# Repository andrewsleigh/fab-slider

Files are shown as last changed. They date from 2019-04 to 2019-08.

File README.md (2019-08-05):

# Fab Slider

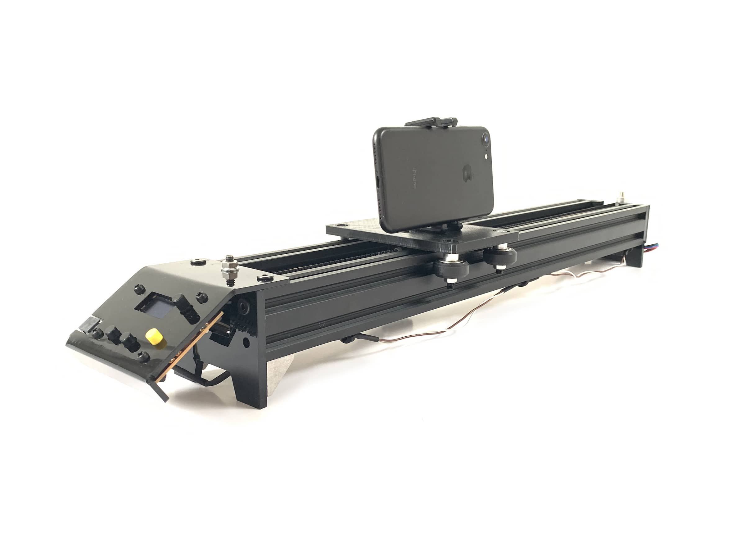
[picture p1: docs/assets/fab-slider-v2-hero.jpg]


A fab-able DIY motorised camera slider

* [The (Arduino Nano) microcontroller, user controls and TMC2130 stepper driver are all integrated onto one board here](boards/driver-arduino-shield/v3)
* [3D and 2D files for the assembly are all here](3d-parts/v1)
* [Arduino sketch here](arduino-code/v2)

This project is designed to be easily replicated, adapted or hacked on by anyone with access to typical fablab tools. 

It's primarily an exercise in learning: how to use a 3D printer; how use an Arduino; how to design circuit boards; how to assemble a machine, and so on. 

So really, it's all about the documentation, which is here:

* <https://andrewsleigh.com/fab-slider/>
* Or see [`docs/_posts/`](docs/_posts/) in this repo

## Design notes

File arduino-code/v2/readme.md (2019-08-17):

# Readme

## Recent changes

Some small modification following testing for version 2.1

* Slowed down timelapse speed range (from min 50 / max 250 to min 2 / max 50
* Changed GUI behaviour to include full information on settings (still non-interactive) while traversing
* Automatically switches directions after hitting end-stop

## State machine

Here is a diagram of the simpler state machine I'm building in this code:

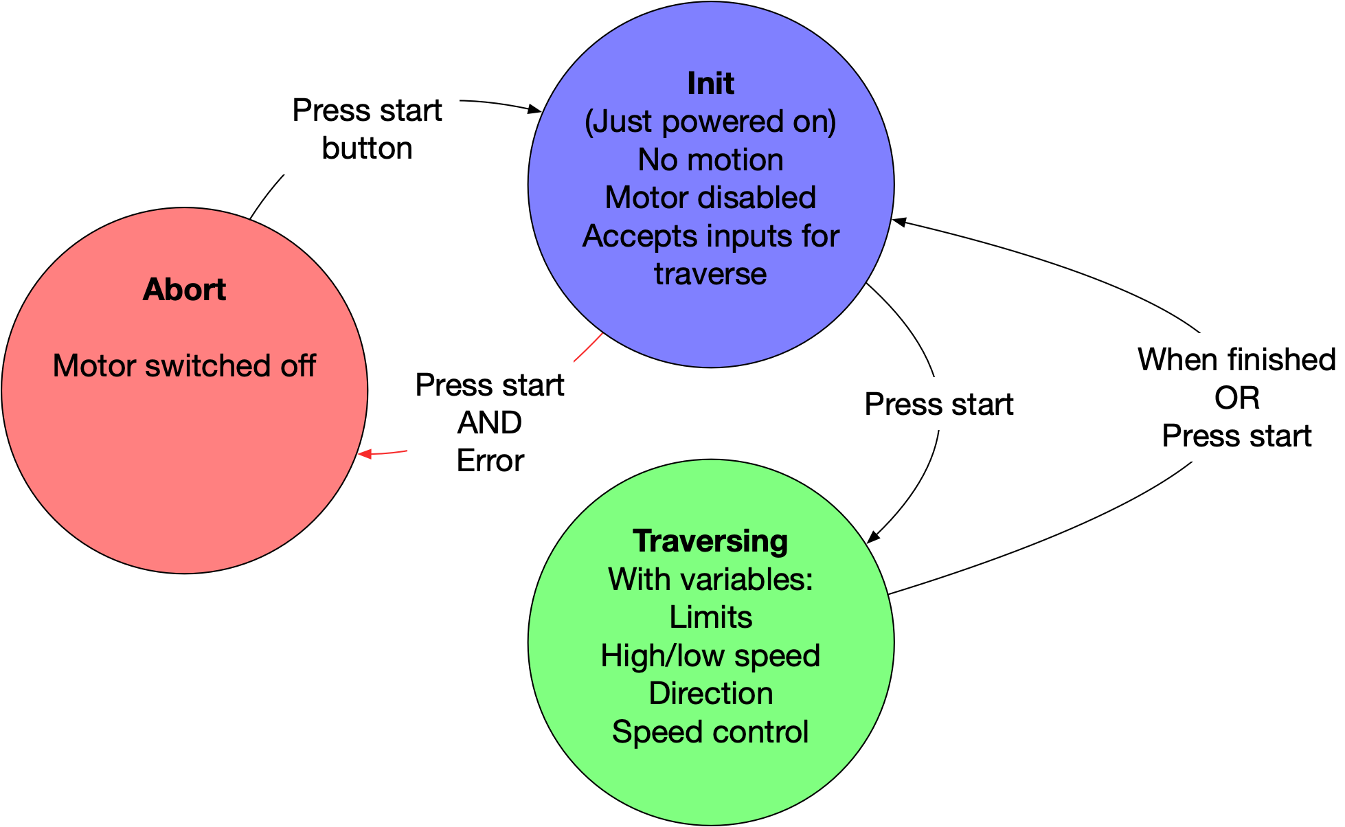
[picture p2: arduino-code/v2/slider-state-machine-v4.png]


<hr/>

This is a lightly documented version of the code for the first release version of my camera slider (v2 in this repo). This is much simplified from the old complex state machine (and quite similar to the v1 code). 

## Libraries

I'm using these Arduino libraries to handle motor control, non-blocking timers, button debouncing and OLED graphics respectively:

```
#include <AccelStepper.h>
#include <neotimer.h>
#include <Bounce2.h>

// OLED
#include <U8g2lib.h>
#include <SPI.h>
#include <Wire.h>
```

## User configuration

The variables that you might want to change are listed at the top of the file so speeds can be tweaked

```
int videoMinSpeed = 500;
int videoMaxSpeed = 5000;
int timelapseMinSpeed = 50;
int timelapseMaxSpeed = 250;
int endStopPadding = 300; // a safe distance to disengage the gantry from the end stops 
```

## Debugging setup

As documented in [Better debugging with the serial monitor](https://andrewsleigh.com/fab-slider/coding-better-debugging/) (or [GitHub link](https://github.com/andrewsleigh/fab-slider/blob/master/docs/_posts/2019-05-12-coding-better-debugging.md)), this section sets up the definitions that allow you to switch serial debugging on and off. You'd want to turn it off in use because sending all that data to the serial monitor interrupts the motion of the stepper.

```
String errorMessage = ""; // this string needs to be initialised even if we're not running debugging

// comment these out to remove debugging
//#define DEBUG // needed for all debugging
//#define DEBUG_TIMER // for messages that print every few seconds
//#define DEBUG_STATE_CHANGE // for messages that print only on a change in the machine state

#ifdef DEBUG

// set up debug timer
Neotimer statusUpdateTimer = Neotimer();

// set up string messages
#define DEBUG_PRINT(str)    \
  Serial.print(str); \
  Serial.print(" ------ ");      \
  Serial.print("In ");    \
  Serial.print(__PRETTY_FUNCTION__); \
  Serial.print(", line: ");      \
  Serial.println(__LINE__);     \

#else
#define DEBUG_PRINT(str) // just leaves an empty definition without serial printing
#endif

```

## Creating objects and variables

After that we just setup all the objects and variables we'll use later. These settings are tweaked for the new shield I designed for an Arduino Nano board and TMC2130 driver.

```
// Accelstepper object
// Revised for nano shield. Format: interface, step pin, direction pin
AccelStepper stepper(AccelStepper::DRIVER, 3, 2);

// Instantiate Bounce objects for buttons
Bounce debouncer_start = Bounce();
Bounce debouncer_mode = Bounce();
Bounce debouncer_direction = Bounce();

// define input/button pin numbers
const int startButtonPin = A3;
const int leftEndStopPin = 6;
const int rightEndStopPin = 5;
const int startFromLeftPin = 7;
const int isTimelapseSpeedPin = 8;

// define output pin numbers
const int motorOffPin = 4;

// define analogue input for speed knob
const int speedPotPin = A2; // revised for nano
int speedInput = 0; // a variable to stare it in
int traverseSpeed = 0; // variable to hold speed when calculated

// variables to determine kind of traverse
bool startFromLeft = true;
bool isTimelapseSpeed = false;

```

## Setup state machine

As part of this, there is a section for the state machine itself:

```
// WARNING: values, order of items and total number of items must match the array below
enum possibleStates {
  INIT,
  TRAVERSING,
  ABORTED
};

// create an array of labels from the enum for debugging
// WARNING: this array must be updated if you change the enum
String stateLabels[3] = {
  "INIT",
  "TRAVERSING",
  "ABORTED"
};

// create a variable of this type
enum possibleStates currentState;

// keep track of whether the state has changed to limit status message updates
bool isNewState;
```

## Initialise OLED Library

My OLED module has I2C pins, so it's important to use the `HW_I2C` keyword in the constructor. I intially used the software I2C mode and it made everything run very slowly. 

Also, after much troubleshooting, I found that I had to initialise the variable that sets the width of the speed indicator on screen up here. If I initialised it inside the `loop()` where I was handling the screen drawing, bad things happened.

```
// OLED library constructor
// Use hardware I2C to avoid code running like treacle
U8G2_SSD1306_128X64_NONAME_2_HW_I2C u8g2 (U8G2_R0, A5, A4);

// instantiate variable to hold width of speed indicator bar. Seems to cuase problems if you create this at the point of use.
float speedBoxWidth = 5;
```

## Setup()

In `setup()` we:
* Set values for the motor
* Set values for the timer
* Open serial comms, if debugging is enabled
* Set up the switches with internal pullup resistors (so they're pulled low to activate)
* Set up output pins for the motor enable function
* Use the debounce library to set up our push-buttons
* Set the starting state, ready for the loop
* Setup the OLED screen ("[This function will reset, configure, clear and disable power save mode of the display](https://github.com/olikraus/u8g2/wiki/u8g2reference#begin)")

```
void setup() {
  stepper.setMaxSpeed(4000); // See https://forum.arduino.cc/index.php?topic=487134.0
  stepper.setAcceleration(2000.0);

#ifdef DEBUG
  Serial.begin(9600); // serial comms for debugging

  // set up  debug message timer
  statusUpdateTimer.set(2000);
#endif

  // initialize the button pins as inputs:
  pinMode(leftEndStopPin, INPUT_PULLUP);
  pinMode(rightEndStopPin, INPUT_PULLUP);

  // initialise output pin
  pinMode(motorOffPin, OUTPUT);

  // Debounced buttons
  debouncer_start.attach(startButtonPin, INPUT_PULLUP); // Attach the debouncer to a pin with INPUT_PULLUP mode
  debouncer_start.interval(25); // Use a debounce interval of 25 milliseconds
  debouncer_direction.attach(startFromLeftPin, INPUT_PULLUP);
  debouncer_direction.interval(25);
  debouncer_mode.attach(isTimelapseSpeedPin, INPUT_PULLUP);
  debouncer_mode.interval(25);

  // set startup state
  currentState = INIT;
  isNewState = true;

  // OLED
  u8g2.begin();
}  
```

## Loop()

Inside the main loop, we first check the state of the push-buttons.

Then we switch through all of the possible machine states, printing any debug messages if required, calling the functions for that state, and checking to see if the push button has been pressed in case we need to switch to a different state. All the OLED drawing is also handled inside this loop 

After the state machine switch, we just check to see if continuous debug messages need to be printed.

```
void loop() {

  // Debounced  buttons
  debouncer_start.update(); // Update the Bounce instance
  debouncer_mode.update();
  debouncer_direction.update();

  switch (currentState) {
    case INIT:

#ifdef DEBUG_STATE_CHANGE
      if (isNewState) {
        printDebugMessages();
        isNewState = false;
      }
#endif

      switchOffMotor();      // disable motor until we need it

      getControlInputs();    // get values for all the motion control variables

      // OLED
      speedBoxWidth = map(analogRead(speedPotPin), 0, 1023, 124, 4); // reverse the reading from the pot because it's wired up the other way around
      // reduce resolution to avoid jittery display
      speedBoxWidth = round(speedBoxWidth / 4);
      speedBoxWidth = speedBoxWidth * 4;

      u8g2.firstPage();
      do {
        u8g2.setFont(u8g2_font_helvB14_tr);
        u8g2.drawStr(0, 14, "Ready");
        u8g2.setFont(u8g2_font_helvB08_tr); // monospace
        // Speed
        u8g2.drawRFrame(0, 22, 128, 16, 3);
        u8g2.drawRBox(2, 24, speedBoxWidth, 12, 1);
        // mode backgrounds
        u8g2.drawBox(0, 42, 62, 15);
        u8g2.drawTriangle(12, 56,  20, 64,  28, 56);
        u8g2.drawBox(66, 42, 62, 15);
        u8g2.drawTriangle(100, 56,  108, 64,  116, 56);
        u8g2.setDrawColor(0);
        if (isTimelapseSpeed) {
          u8g2.setCursor(70, 53); // different padding for each string
          u8g2.print("Timelapse");
        } else {
          u8g2.setCursor(82, 53);
          u8g2.print("Video");
        }

        u8g2.setCursor(13, 53); // add some padding to the left
        if (startFromLeft) {
          u8g2.print("L >> R");
        } else {
          u8g2.print("R >> L");
        }

        u8g2.setDrawColor(1); // reset color
      }

      while ( u8g2.nextPage() );

      if ( debouncer_start.fell() ) {
        // first, check both end stops are connected and not currently closed

        // if ((!startFromLeft && digitalRead(leftEndStopPin) == HIGH) || (startFromLeft && digitalRead(rightEndStopPin) == HIGH)) {
        // The problem with this error check is that the traverse will stop as soon as it hits an end stop.
        // Easier just to force the user to move gantry off end stop at start

        if (digitalRead(rightEndStopPin) == HIGH || digitalRead(leftEndStopPin) == HIGH) {
          switchOffMotor; // just in case
          errorMessage = "End stop closed, or not connected";
          currentState = ABORTED;
          isNewState = true;
        } else { // otherwise, it's safe to start traverse

          // OLED
          // This is a bit of a hack. Ideally you'd write to the screen inside the traverse state.
          // But doing it here, just before entering that state, avoids interfering with motion

          u8g2.firstPage();
          do {
            u8g2.setFont(u8g2_font_helvB14_tr);
            u8g2.drawStr(0, 24, "Traversing");
          } while ( u8g2.nextPage() );

          currentState = TRAVERSING;
          isNewState = true;
        }
      }
      break;

    case TRAVERSING:

#ifdef DEBUG_STATE_CHANGE
      if (isNewState) {
        printDebugMessages();
        isNewState = false;
      }
#endif

      switchOnMotor();

      if ( debouncer_start.fell() ) {
        currentState = INIT;
        isNewState = true;
      }

      traverse();
      break;

    case ABORTED:

#ifdef DEBUG_STATE_CHANGE
      if (isNewState) {
        printDebugMessages();
        isNewState = false;
      }
#endif

      // OLED
      u8g2.firstPage();
      do {
        u8g2.setFont(u8g2_font_helvB14_tr);
        u8g2.drawStr(0, 14, "Error");
        u8g2.setFont(u8g2_font_helvR14_tr);
        u8g2.drawStr(0, 42, "Is gantry");
        u8g2.drawStr(0, 62, "at end stop?");

      } while ( u8g2.nextPage() );

      switchOffMotor();

      if ( debouncer_start.fell() ) {
        currentState = INIT;
        isNewState = true;
      }

      break;

  }

  // program-wide debug status messages
  // runs continuously on a timer
#ifdef DEBUG_TIMER
  if (statusUpdateTimer.repeat()) {
    printDebugMessages();
  }
#endif

}
```

## Other functions

These functions are called from different states within the main loop. 

I only want to get the speed, direction and mode inputs when the slider is not moving; that way any unintentional changes don't affect motion while you're recording. 

```
void getControlInputs() {

  // TIMELAPSE OR VIDEO MODE
  // revised for shield v3
  // now I'm using momentary buttons to toggle modes and display the current moe on the screen
  if ( debouncer_mode.fell() ) {
    isTimelapseSpeed = !isTimelapseSpeed;
  }

  // SET DIRECTION
  if ( debouncer_direction.fell() ) {
    startFromLeft = !startFromLeft;
  }

  // SPEED CONTROL
  speedInput = map(analogRead(speedPotPin), 0, 1023, 1023, 0); // reverse the reading from the pot because it's wired up the other way around

  // map the speed set on the knob to useful values
  if (isTimelapseSpeed) { // test to see if we're running in timelapse or video mode
    traverseSpeed = map(speedInput, 0, 1023, timelapseMinSpeed, timelapseMaxSpeed);
  } else {
    traverseSpeed = map(speedInput, 0, 1023, videoMinSpeed, videoMaxSpeed);
  }

  // test to see if we're running L-R or R-L
  if (!startFromLeft) { // if NOT startFromLeft
    traverseSpeed = -traverseSpeed; // Left is negative, so if we start from the left, speed must be positive!
  }
}
```

For the motion itself, I'm using the AccelStepper library. I documented some of my trials with that [here](https://andrewsleigh.com/fab-slider/coding-accelstepper/): 

```
void traverse() {

  stepper.setSpeed(traverseSpeed);
  stepper.runSpeed();

  if (digitalRead(leftEndStopPin) == HIGH) { // if it touches left end-stop
    DEBUG_PRINT("Hit left end stop");
    // move off the end stop
    stepper.runToNewPosition(stepper.currentPosition() + endStopPadding); // Blocks until stepper is in position
    errorMessage = "Finished traverse";
    currentState = INIT;
    isNewState = true;
  }

  if (digitalRead(rightEndStopPin) == HIGH) { // if it touches right end-stop
    DEBUG_PRINT("Hit left end stop");
    // move off the end stop
    stepper.runToNewPosition(stepper.currentPosition() - endStopPadding); // Blocks until stepper is in position
    errorMessage = "Finished traverse";
    currentState = INIT;
    isNewState = true;
  }
}
```

It's pretty easy to switch off power to the motor by pulling the ENABLE pin high:

```
void switchOffMotor() {
  digitalWrite(motorOffPin, HIGH);
}

void switchOnMotor() {
  digitalWrite(motorOffPin, LOW);
}
```

And finally there's a function handle printing the current stus to the serial monitor:

```
void printDebugMessages() {
#ifdef DEBUG
  Serial.println("\n--------------------   ----------");
  // machine state
  Serial.print("Current state:         ");
  Serial.println(stateLabels[currentState]);

  // latest error message
  if (errorMessage != "") {
    Serial.print("Last message:          ");
    Serial.println(errorMessage);
  }

  // control settings
  Serial.print("Start from:            ");
  if (startFromLeft == 1) {
    Serial.println("Left");
  } else {
    Serial.println("Right");
  }
  Serial.print("Mode:                  ");
  if (isTimelapseSpeed == 1) {
    Serial.println("Time-lapse");
  } else {
    Serial.println("Video");
  }
  Serial.print("Speed:                 ");
  Serial.println(traverseSpeed);
  Serial.println("--------------------   ----------\n");
#endif
}
```

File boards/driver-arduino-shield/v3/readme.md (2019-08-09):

# Readme

<!-- ![IMG_2599.jpg](IMG_2599.jpg) -->

This is version 3 of a board to use a stepper driver (a TMC2130) with an Arduino Uno to control a stepper motor for a <a href="https://andrewsleigh.com/fab-slider/">camera slider</a>.

The front (copper side) of the board, with all traces and user-facing components:

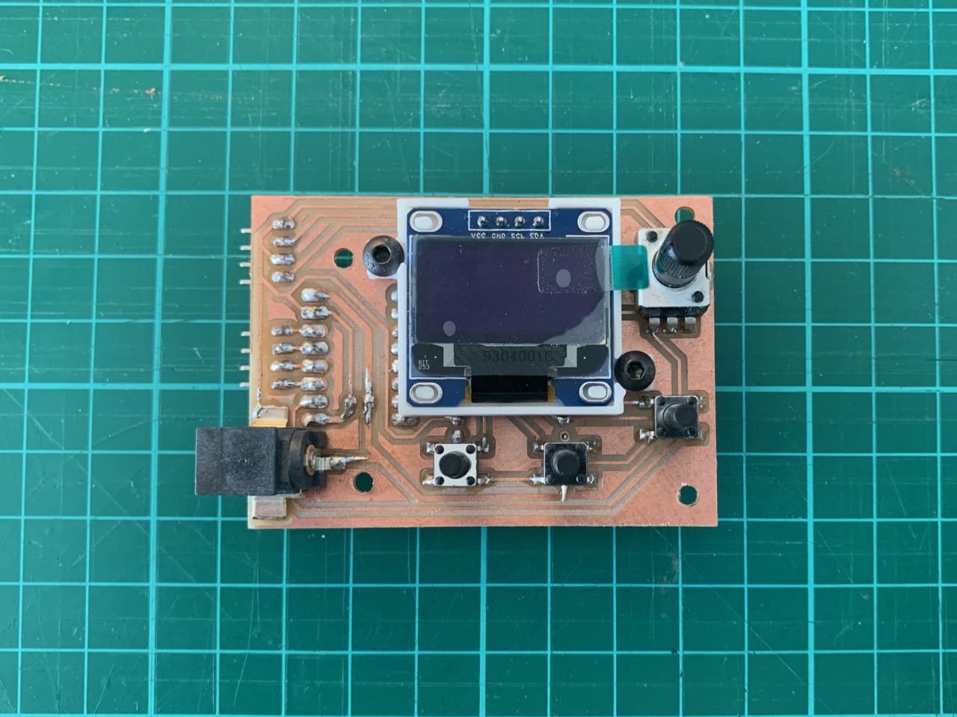
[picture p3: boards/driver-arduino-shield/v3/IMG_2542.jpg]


The back side of the board, which just has female headers for the Nano and driver module, and male headers for connections to the motor and end stops:

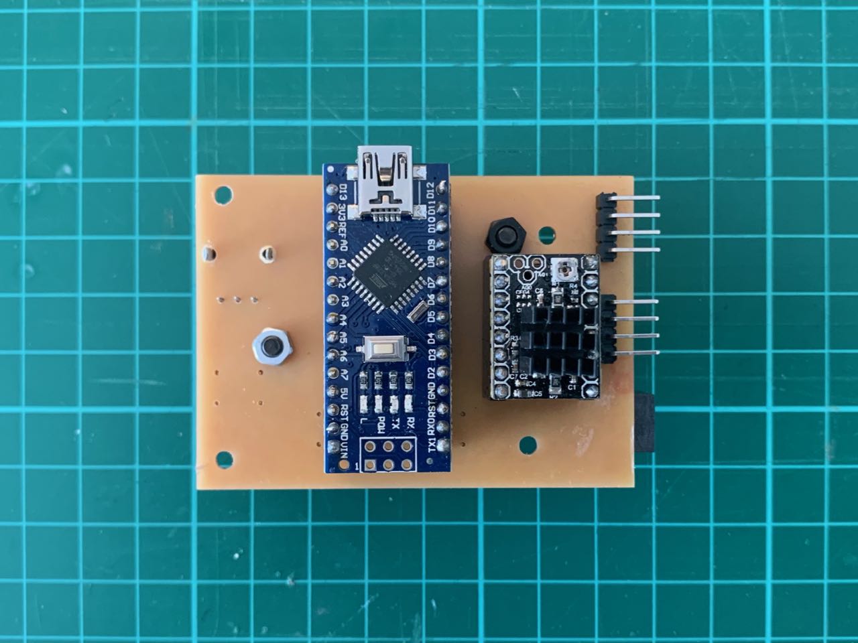
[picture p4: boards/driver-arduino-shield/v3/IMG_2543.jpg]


(Not visible here is the smoothing capacitor underneath the driver module.)

## Layout diagrams

### Front

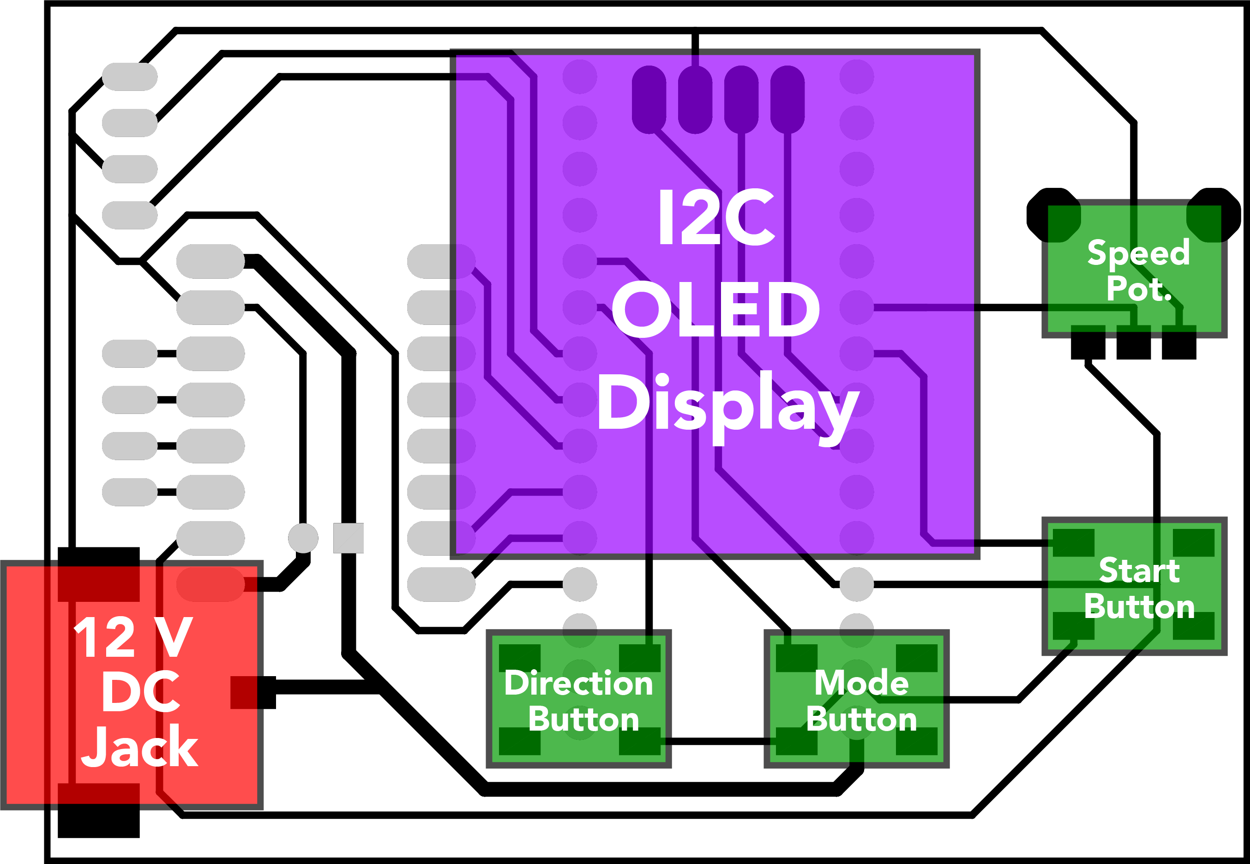
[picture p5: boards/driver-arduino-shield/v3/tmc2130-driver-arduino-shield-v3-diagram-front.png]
Front


### Back

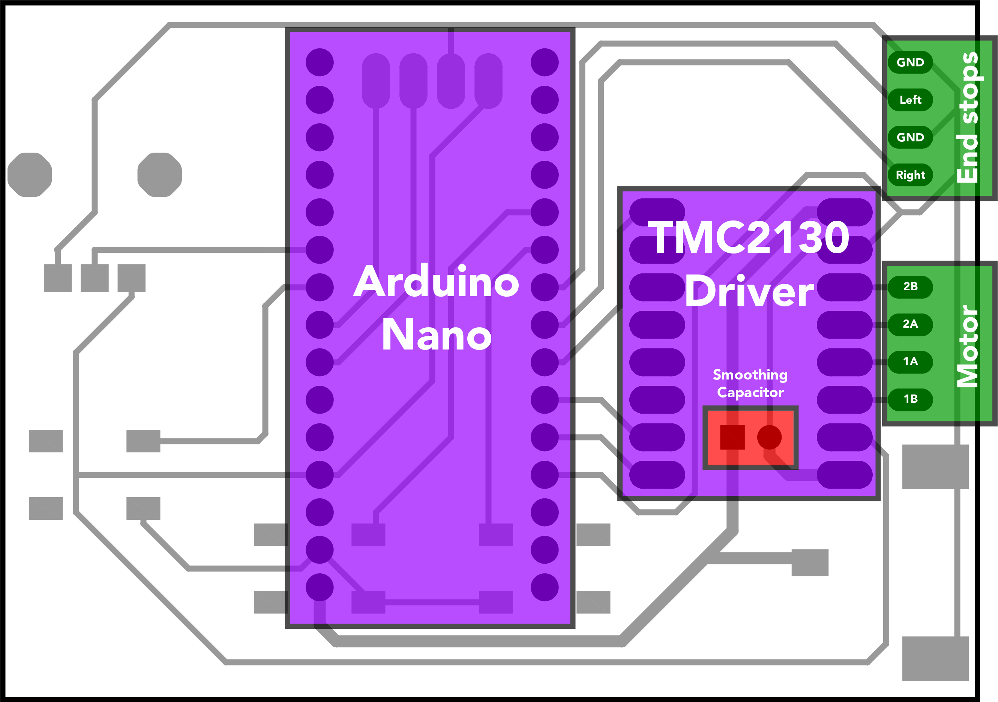
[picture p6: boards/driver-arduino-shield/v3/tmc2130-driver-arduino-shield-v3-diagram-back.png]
Back


This is the release version of the board design. It works with the release version of the Arduino code at [../../../arduino-code/v2](../../../arduino-code/v2).

As well as the passive components, you'll need an Arduino Nano, an I2C 128x64 OLED module and a TMC2130 stepper driver. The code could be adapted to work with an A4988-based driver, which should be compatible with this board.

The full story of how I came to this board design is documented in the [journal](https://andrewsleigh.com/fab-slider/), in particular:

* [Designing a new stepper driver and controls board](https://andrewsleigh.com/fab-slider/v2-shield/) (v2)
* [Designing a new board — again](https://andrewsleigh.com/fab-slider/v3-shield/) (v3)

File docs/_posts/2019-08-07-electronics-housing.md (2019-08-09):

---
permalink: electronics-housing/
title: Electronics housing
date: 2019-08-07
author: Andrew
layout: page
sort_id: 93
sort_tag: v2_design
---

I probably spent more time on this aspect of the build than any other part. As I changed the shield design, I prototyped different cases, but could never get them down to a reasonable size. 

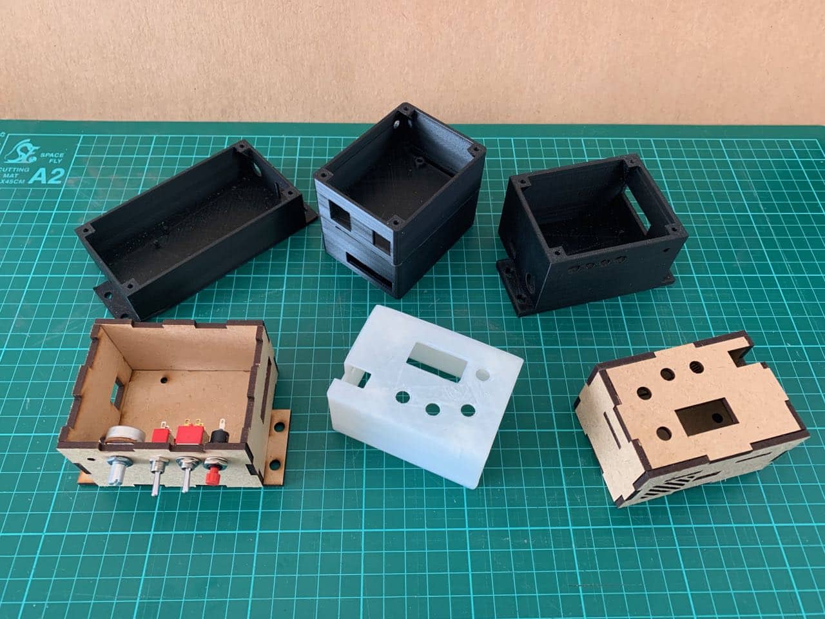
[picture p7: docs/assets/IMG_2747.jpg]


### Mounting to the main structure of the slider

I want the whole thing to be one object, but there are very few possible mounting options for the electronics. I originally thought I could mount it to the side, but after making several prototypes based on this assumption, I realised that it would interfere with the gantry. An obvious mistake in retrospect.

After I switched to a [single 2-sided board design](../v3-shield), I was able to get the size of the electronics down enough that end-mounting was possible.

### Making assembly possible

The biggest problem with the housing is putting it all together. The housing itself has to be mounted to the frame. The board has to be put into, and then fixed to, the housing. The controls, if separate, need to be fixed to the housing, and then connected to the board. And then a lid or screen needs to be fixed to close everything off.

Satisfying all these requirements at the same time was very difficult, and forced me to simplify my board design, in particular so that the controls are fixed to the board, not the panel.

### Mounting posts and plates

I tried various 3D-printed cases with short pillars with 3 mm holes onto which the board could be screwed with M3 machine screws. I couldn't bolt screws through from the outside of the case, because I wanted it to be flush, and with a 2-3 mm case thickness, there wasn't enough room to add a rebate for the screw head.

However, I wasn't able to print with good enough fidelity and tolerances to make that work with M3 machine screws. In retrospect, using self-tapping screws would have likely worked. This is often how boards are mounted onto plastic cases in commercial products.

I also tried a version (prototype pictured below) with a mounting plate inside the enclosure but it was very difficult to get this compact enough to be viable, while still allowing room for all the parts to be put into the case.

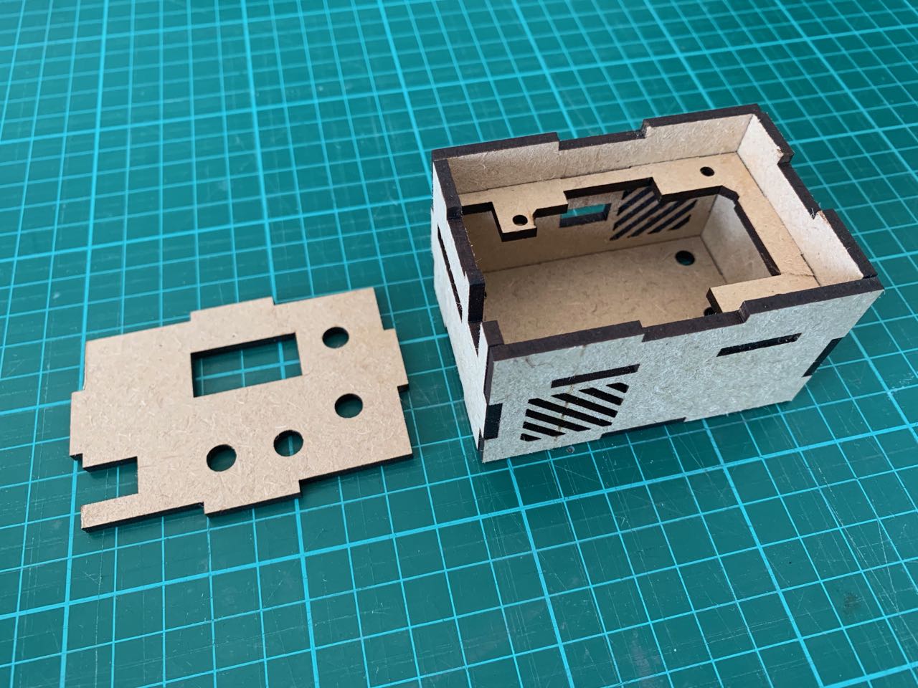
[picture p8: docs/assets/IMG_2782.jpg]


### Ventilation

The TMC2130 driver has a pretty large heatsink (relative to the A4988 drivers) and the documentation recommends fan-assisted cooling. I suspect this may be more of an issue if you're using it to drive a 3D printer, but still, I wanted to include some passive ventilation at least.

### Connections outside the casing

While the electronics are as integrated as possible, some connections do need to be made to other parts of the machine, specifically, to the end-stop switches and the motor. I included 2 right-angle male headers on the board to enable this, and positioned them so an opening could be made in the case for connection.

## Switching to a faceplate housing

Inspired by the design of the [Creality Ender 3](https://www.creality3d.shop/products/creality3d-ender-3-pro-high-precision-3d-printer), I decided to try mounting the electronis to a faceplate, and leaving them unenclosed on the other sides. 

I cut a plate from 3 mm black acrylic, and bent it to shape with the help of some pieces of MDF, a vice and a heat gun. While a simple couple of folds, I was pleased with how easy it was to control this and get a good result, even with these primitive tools.

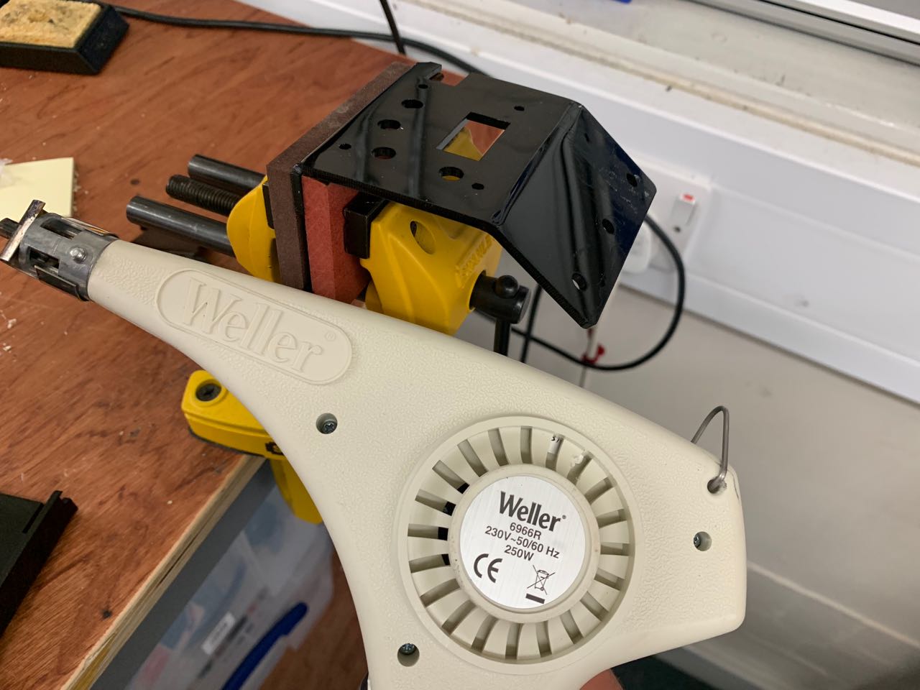
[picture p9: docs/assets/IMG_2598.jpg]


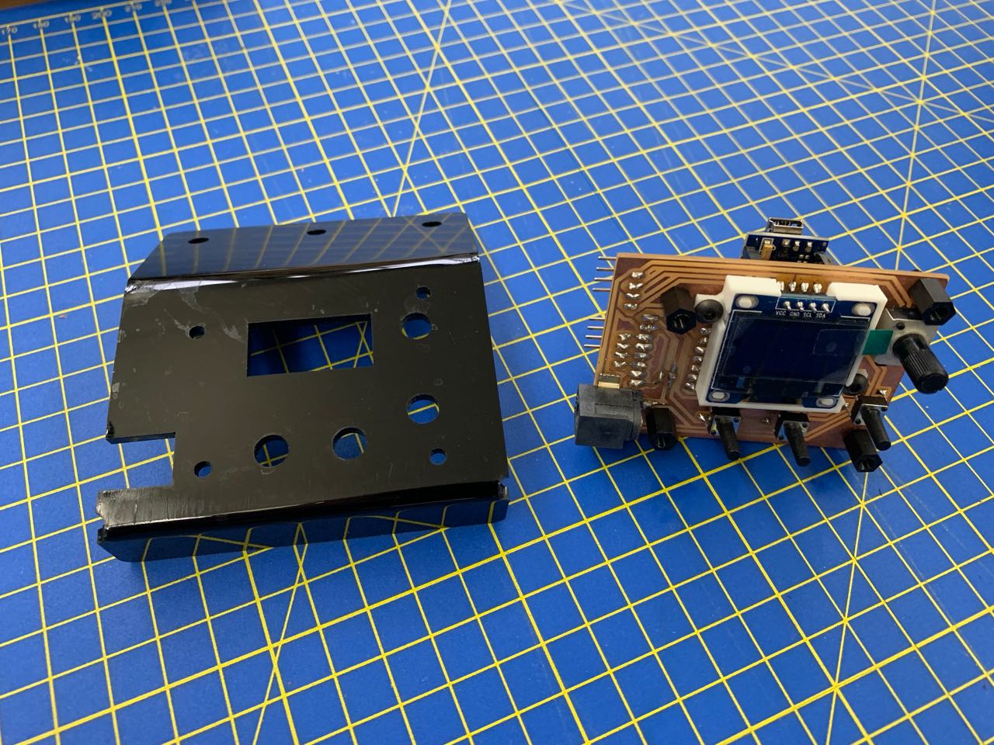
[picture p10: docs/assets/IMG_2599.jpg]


This has two mounting holes on top so it can be fitted to the rails, and one central hole on top to take the idler pulley, which was previously attached to a separate plate here.

I'm very happy with this design, which is a lot more elegant than my previous attempts, and offers plenty of ventilation(!), perhaps at the expense of a little protection. 

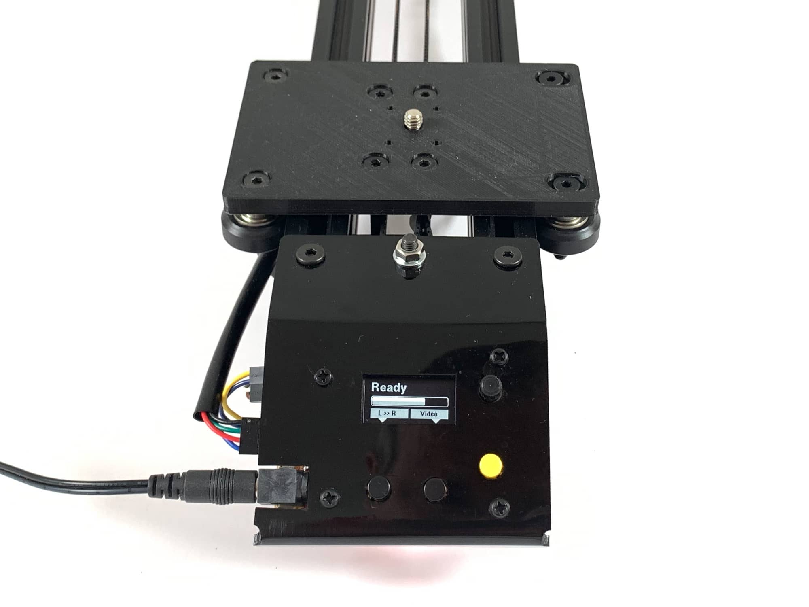
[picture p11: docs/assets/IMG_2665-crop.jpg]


The faceplate design and OLED display mount are in the Git repo:
[fab-slider/3d-parts/v1/electronics-face-plate](https://github.com/andrewsleigh/fab-slider/tree/master/3d-parts/v1/electronics-face-plate)

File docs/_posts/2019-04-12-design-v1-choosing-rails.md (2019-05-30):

---
permalink: design-v1-rails/
title: Aluminium extrusion rails
date: 2019-04-12
author: Andrew
layout: page
sort_id: 31
sort_tag: v1_design
---

The rails provide the main structure of the slider, and are also the guide surface along which the gantry slides.

I want to use standardised aluminium extrusion for the rails. This provides the best balance of reproducibility and quality. Aluminium extrusion is widely available, cost effective, standardised and high-quality. This is a good guide to aluminium extrusion: [Beginner’s Guide to Building Things With V-Slot Aluminum Extrusion](https://www.makeuseof.com/tag/beginners-guide-building-things-v-slot-aluminum-extrusion/).

## Choosing a profile
There are different kinds of profile. The two main profiles seems to be B-Type and I-Type (__Bosch Rexroth__ and __Item__ respectively). The B-type profile has a stepped slot, whereas the I-type has a smooth curve.

They also differ in other areas. For example RS Components' [I-type 'RS-Pro' extrusion](https://uk.rs-online.com/web/p/tubing-struts/8508476/) has a 5 mm groove, and a 4.3 mm central hole, which can be tapped for a 5 mm thread. They also have Bosch Rexroth extrusion with a 6 mm groove and a 5.5 mm central hole.

There is also a newcomer to the field: V Slot. As the name suggests, this has a straight V-shaped bevel. This is an open source design, and ideal to take wheels, as it provides a flat even surface for them to roll against. It also has holes that can be tapped for M5 bolts.

## Choosing size

I suspect two 2020 profile rails will be enough for this small span. 2040 mounted vertically would give me more rigidity. And the [8040 C Beam](https://ooznest.co.uk/product/c-beam-linear-rail-cut-to-size/) would be even more rigid:

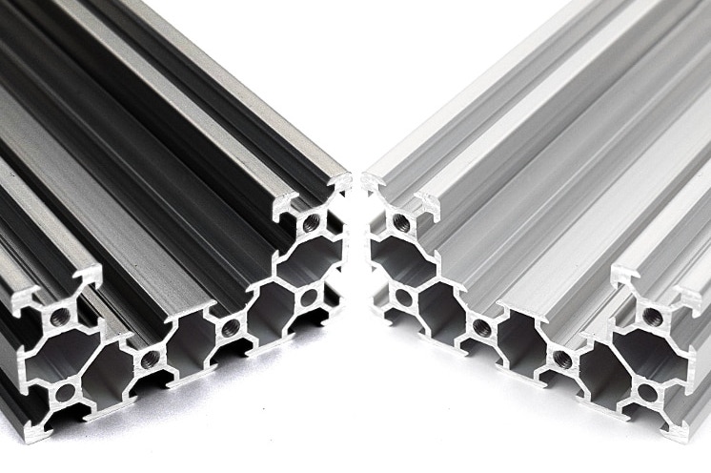
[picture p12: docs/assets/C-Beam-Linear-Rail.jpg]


Ooznest has a [guide to help you estimate deflection](https://ooznest.co.uk/wp-content/uploads/2018/05/How-To-Estimate-Deflection.pdf). In my case, the calculation looks like this:

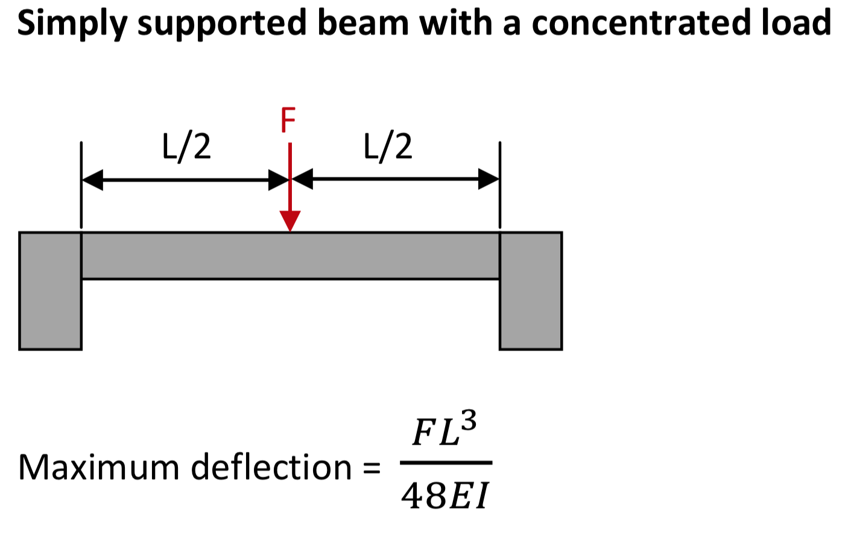
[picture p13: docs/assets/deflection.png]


Let's plug in some numbers:

* Mass of the load: 1kg (roughly, for an SLR camera)
* F = Mass x Gravity = 1 * 9.81 = 9.81N
* L = 0.5m
* I (moment of inertia) = 6.988 * 10<sup>-9</sup> (for 2020 profile)
* E (modulus of elasticity) = 68.9 GPa (gigapascals) =  68.9 * 10<sup>9</sup> Pa

Therefore deflection  
= (9.81 * (0.5)<sup>3</sup>) / (48 * 68.9 * 10<sup>9</sup> * 6.988 * 10<sup>-9</sup>)  
= 1.22625 / 23110.7136  
= 0.000053 m  
= 0.053 mm  

So nothing to worry about at this length. However, if I made a 1 m long slider, deflection under ideal conditions for a 1 kg load would come out at: 9.81 / 23110.7136 = .00042 m = .42 mm. So for that span it might be worth using a more rigid profile.

However, there is one other advantage to a larger profile such as 2040. That has two holes at each end, allowing for more robust assembly. I'm concerned that the 2020, with only one hole at each end might twist in the assembly, causing the gantry to move poorly.

## Choosing length

While a bigger slider is always more useful, a smaller one is cheaper, and easier to store, so I think a better target for a first build. If I decide to remake it, I can always disassemble the first version and re-use some parts for a bigger one.

## Prices

[2 x 50 cm 2020 V-Slot from Ooznest](https://ooznest.co.uk/product-category/parts/mechanical-parts/v-slot-extrusions/): £9.60 + postage

[2 x 50 cm 2020 IR Range Aluminium Profile (I-type) from KJN](): £7 + postage

[50 cm 8040 C-Beam from Ooznest](https://ooznest.co.uk/product/c-beam-linear-rail-cut-to-size/): £14.80 + postage (both ends tapped with 5mm holes: £16.24. I should be able to tap these myself if needed). I like this, but it's not a standard profile,

[1 m I-type from RS Components](https://uk.rs-online.com/web/p/tubing-struts/8508476/): £6.90 + postage

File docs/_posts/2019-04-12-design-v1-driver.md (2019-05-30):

---
permalink: design-v1-driver/
title: Stepper motor driver
date: 2019-04-12
author: Andrew
layout: page
sort_id: 33
sort_tag: v1_design
---

I don't know if it's actually possible to drive a stepper motor directly from an Arduino, but certainly all the projects I've seen use a separate driver chip on another board that can be connected to the microcontroller.

### Motor driver

There are lots of different boards, based on different chips. So how do you choose?

From [How to Make a Robot - Lesson 5: Cho - RobotShop Community](https://www.robotshop.com/community/tutorials/show/how-to-make-a-robot-lesson-5-choosing-a-motor-controller)

> 1 Is the motor you selected unipolar or bipolar? Choose a stepper motor controller type accordingly, though a growing number are able to control both types. The number of leads is usually a dead give-away of the motor type: if the motor has 4 leads, then it is bipolar; should it have 6 or more leads, then it is unipolar.
> 2 Choose the motor controller voltage range to match your motor’s  nominal voltage .
> 3 Find out how much current per coil your motor requires, and find out how much current (per coil) the stepper motor controller can provide.If you cannot find the current per coil, most manufacturers list the coil impedance, R . Using Ohms Law (V=IR), you can then calculate the current (I).
> 4 As with DC motor controllers, the control method is an important consideration.

From [Stepper Motor Control - Adafruit Motor Selection Guide](https://learn.adafruit.com/adafruit-motor-selection-guide/stepper-motor-control):

> Stepper motor controllers are more complex than DC motor controllers. Driving a bipolar motor with microstepping requires 2 complete H-bridges and 2 channels of PWM.
>
> The versatile Adafruit Motor Shield V2 has 4 H-bridges and can drive as many as 2 steppers. What’s more, it is stackable to control dozens of motors.

From [Driving a Stepper - All About Stepper Motors - Adafruit](https://learn.adafruit.com/all-about-stepper-motors/driving-a-stepper#simple-dual-h-bridge-driver-3-8):

> Simple Dual H-Bridge Driver
> Driving a bipolar motor requires 2 full H-bridges so it can reverse the current to the phases. H-bridges can be tricky to build from scratch. But there are plenty of H-bridge chips available to simplify the task.>
> The L293D is one of the most popular and economical chips. These can be found at the heart of most first-generation motor shields, including the incredibly popular V1 Adafruit Motor Shield.

The motors I'm looking at are bipolar, with 4 leads, and run at 12 V and 0.33/0.35 A.

It looks like an [Allegro 3967](https://cdn.sparkfun.com/datasheets/Robotics/A3967-Datasheet.pdf)-based driver board should work. This chip is rated to ±750 mA, 30 V

* This is the basis of the Sparkfun [Easy Driver](https://www.sparkfun.com/products/12779) ($15)
* SeeedStudio also have a similar board: [Stepper Motor Driver V4.5](https://www.robotshop.com/en/seeedstudio-stepper-motor-driver-v45.html) ($13)

This board design is open source ([documented here](https://www.schmalzhaus.com/EasyDriver/)), so I could, for version 2, fab my own using this chip. Perhaps with an integrated microcontroller. It also means there are numerous cheaper knock-offs available:

* [EasyDriver Stepper Motor Controller A3967](https://www.robotshop.com/uk/easydriver-stepper-motor-controller-a3967.html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) (£5.70)
* [This on Amazon](https://www.amazon.co.uk/Aihasd-EasyDriver-Stepper-Development-Arduino/dp/B00WR8IQHW) (£2.80)
* [This on eBay](https://www.ebay.co.uk/p/EasyDriver-Shield-Stepping-Stepper-Motor-Driver-V44-A3967-for-Arduino/2169027753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) (£1.30)

There is another Allegro chip, the [A4988](https://cdn.sparkfun.com/datasheets/Robotics/A4988-Datasheet.pdf), which is rated to 35 V and 2 A.

* This is used in Sparkfun's [Big Easy Driver](https://www.sparkfun.com/products/12859) ($20)
* Pololu also have a much cheaper board: [A4988 Stepper Motor Driver Carrier](https://www.pololu.com/product/1182) $6

Adafruit have a nice board, the [Motor/Stepper/Servo Shield for Arduino v2 Kit - v2.3](https://www.adafruit.com/product/1438), based on the TB6612, which can drive up to two steppers at 1.2 A per channel. This is $20, so comparable to other brand-name boards that can only drive one stepper.

There are many others, including the [STMicroelectronics L293D](http://www.st.com/st-web-ui/static/active/en/resource/technical/document/datasheet/CD00000059.pdf) used in the [Adafruit Arduino Motor Shield](http://www.adafruit.com/index.php?main_page=product_info&products_id=81) and [Toshiba TB6600](http://www.semicon.toshiba.com.cn/info/docget.jsp?type=Catalog1&lang=en&pid=TB6600HG) used in the [PiBot TB6600 Stepper Driver](http://reprap.org/wiki/PiBot_TB6600_Stepper_Driver) and also in the _fab-able_ [satstep6600](https://github.com/satstep/satstep6600).

[Reprap also has a good list of different driver chips.](https://reprap.org/wiki/Stepper_motor_driver)

I went with a generic A4988-based board, originally one from Ooznest, which I fried, and then one from Elegoo ([£11 for 5 boards](https://www.amazon.co.uk/Stepper-Stepstick-Headsink-Arduino-Machines/dp/B07B9ZKST7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)). This is a clone of the RepRap [StepStick board](https://reprap.org/wiki/StepStick).

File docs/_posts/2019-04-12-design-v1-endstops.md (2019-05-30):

---
permalink: design-v1-endstops/
title: Endstops
date: 2019-04-12
author: Andrew
layout: page
sort_id: 37
sort_tag: v1_design
---

There needs to be some way to put power to the motor when the gantry reaches the end of its travel. It may also be useful to have a way of calibrating the slider so it knows where its endpoints are. This is what end-stops are for.

## Examples

Via <https://hackaday.com/2017/03/30/endstops-that-stay-out-of-the-way/>:

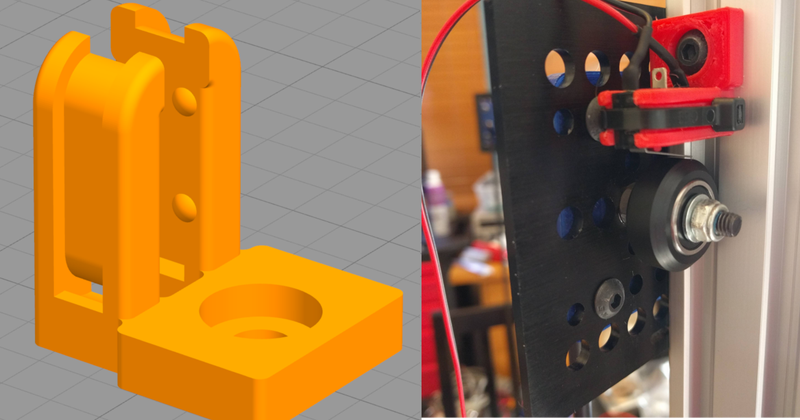
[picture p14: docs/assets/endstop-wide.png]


<https://www.thingiverse.com/thing:2204123>

> It is designed to be triggered by the third wheel of a three wheel carriage. When used in this way, the endstop does not waste any space on the linear motion, since the carriage plate edge can travel completely past it.  

Notice the alignment of the lever - it’s 90&deg; from the rail, pointing into the cavity. Aligned with the wheel. So the whole thing fits against the V-groove, and can be triggered by the wheel itself, which rides in the same groove.

For maximum travel, could I mount my stops in the end plates, in the same orientation?

Looks like a friction fit base on the two fingers of the clip being pressed together by the cable tie.

From <http://marlinfw.org/docs/hardware/endstops.html>:
I think this is a Makerbot design, which incorporates capacitor and resistor as a hardware filter against noise, but also mounts the switch on a board with decent mounting holes.

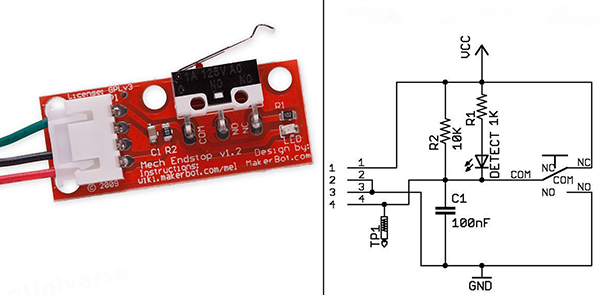
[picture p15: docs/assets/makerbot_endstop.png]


<https://www.thingiverse.com/thing:2230378>

A simple design, but this would need some very small (M2?) bolts to go through the switch casing.

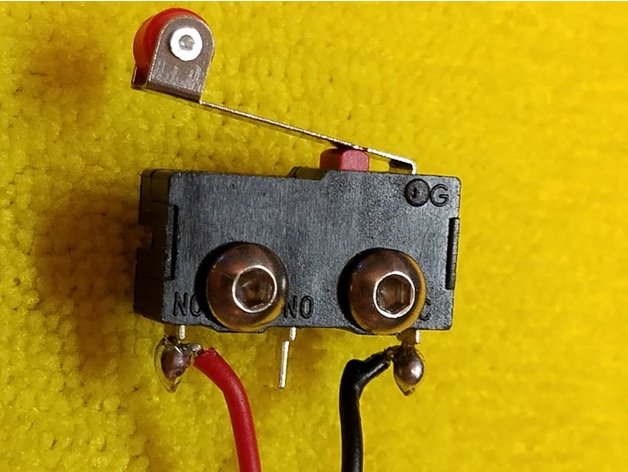
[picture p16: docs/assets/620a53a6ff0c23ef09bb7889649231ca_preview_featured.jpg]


## Running cables back
I might need to print some little cable clips that find into underside of V-slot to trail wires back from far end end-stop back to electrical parts at the other end.

## Electrical issues

I also need to deal with interference, denouncing, and possibly the resistance of the motor - how quickly can it be stopped?

From <http://marlinfw.org/docs/hardware/endstops.html>

> Endstops and Electromagnetic Interference (EMI)  
> Electromagnetic Interference (EMI) or electric noise, is an effect which can ruin the clean signal needed to properly and precisely measure electronically, be it temperature, endstop hits or any other value.  
>   
> In today’s life an abundance of sources for Electric Noise exists: Mobile phones, microwaves, WIFI, power supplies etc. In a 3D printer itself, there are also some prominent and strong sources of such noise:  
> * Heated beds  
> * Hot ends  
> * Stepper motors  
> * PWM modulation  
> The Electromagnetic Interference created by these sources are picked up by other components, either because they are directly connected or via radiation. The useful signal needed by the other components will be disturbed or even altered so much that it is no longer useful.  

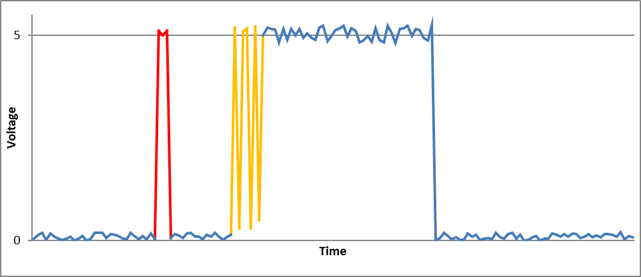
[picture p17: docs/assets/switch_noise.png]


> Endstop with capacitor  
> A more simple variant, that can easily be fitted to existing endstops is a 100nF capacitor, soldered over the two endstop connector pins (in parallel):  

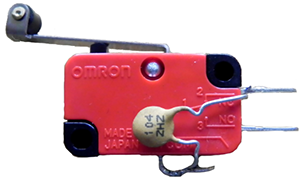
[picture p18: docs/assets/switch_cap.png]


## What to do when you hit the switch?

### Stop the servo!

Maybe also stop drawing power – since even a stopped servo draws power.

### Pull back a bit…

From <https://www.instructables.com/id/End-Stop-Limit-Switch-Problems/>

> Another handy tip, if your using the  [omron lever style limit switches](http://3dtek.xyz/products/cnc-3d-printer-limit-switches) , set the pull off constants in grbl to about 5mm so that when your homing finishes it pulls back off the limits when done so that its not bending the levers so much, otherwise you constantly have to re bend them back out.

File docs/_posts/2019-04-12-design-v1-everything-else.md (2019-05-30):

---
permalink: design-v1-everything-else/
title: Everything else
date: 2019-04-12
author: Andrew
layout: page
sort_id: 38
sort_tag: v1_design
---

I will also need to design and make/buy a load of other things, which I haven't thought through fully yet.

## End caps / feet

A way to hold the rails together and also provide a stable base on (possibly uneven) surfaces

## Controls and screen

<span class="wip">WIP</span> I don't know what controls I'll need, or if I'll need to get any feedback.

## End stops

I have some end-stop switches left over from a previous project. These will need to be mounted onto the rails and connected to the microcontroller.

## Tripod mount

This is a 'nice-to-have' feature, but shouldn't be difficult to implement. I just need a plate on the bottom of the rails with a threaded hole (or captured nut) to accept a 1/4" (or possibly 3/8") UNC threaded bolt. These are the [standard sizes for tripod mounts](http://www.photokonnexion.com/photography-thread-size/):

| Diameter (inch) | Diameter (mm) | Thread size |
| :---: | :---: | :---: |
| 1/4 | 6.3500 | 20 |
| 3/8 | 7.9375 | 16 |

## Assembly brackets and casings

### Motor

There are many [3D designs on Thingiverse](https://www.thingiverse.com/search?q=nema+17+bracket&dwh=1005cb30d3341f54).

The sketch at the top of the page shows the bare minimum I'd need to do to mount the motor to the rails in the right orientation. This needs more work, perhaps in Fusion 360.

### Belt bearing

Unless I use an idler pulley (which has fences on either side of the rail), this might need some sort of guides to stop the belt sliding off the bearing.

Ideally, (as on the Adafruit slider bearing bracket) the bolts in this bracket should fit into slots, so the bracket itself can be moved back and forth to adjust belt tension (just like the rear wheel on a single speed bike).

### Microcontroller and driver boards

I think for version 1, this could be an entirely separate assembly, since only an electrical connection is needed between the boards and the motor.

## Fixings

It would be nice if the design could standardise on one bolt size, say M5, with one head type. For example, if all bolts had Allen key heads of the same size, you could attach the correct key somewhere on the frame of the machine, for easy adjustment

I may also need T-nuts and brackets to connect other parts of the sytem to the rails.

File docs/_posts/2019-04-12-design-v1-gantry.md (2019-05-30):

---
permalink: design-v1-gantry/
title: Gantry
date: 2019-04-12
author: Andrew
layout: page
sort_id: 36
sort_tag: v1_design
---

The gantry is basically just a flat plate with mounting holes for attaching different devices, and for the wheels and timing belt.

Ooznest sell an [aluminium gantry plate](https://ooznest.co.uk/product/c-beam-gantry-plate-kit/)for the 8040 V-slot C-beam (in a kit form with delrin wheels for £25). This C-beam has a 40 mm channel down the middle, so it should be adaptable for two lengths of 2020 mounted 40 mm apart.

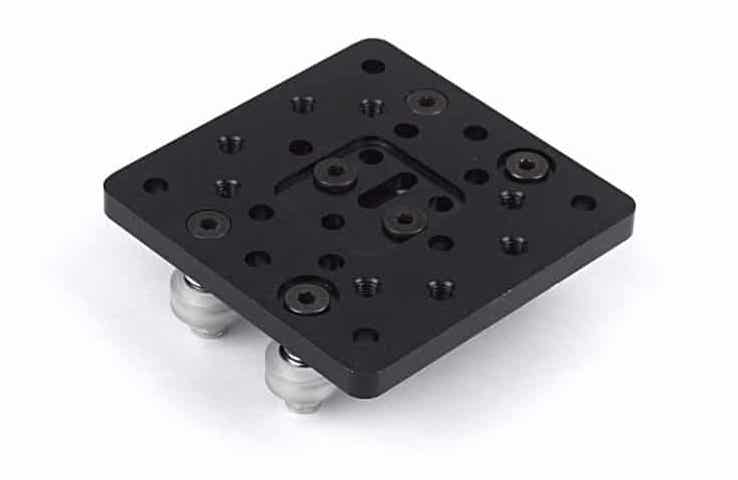
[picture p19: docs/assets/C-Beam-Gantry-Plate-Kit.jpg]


They also have a [simpler plate](https://ooznest.co.uk/product/v-slot-gantry-plate-small-kit/) designed to straddle a single 2020 rail. (£24 in a kit with 4 wheels).

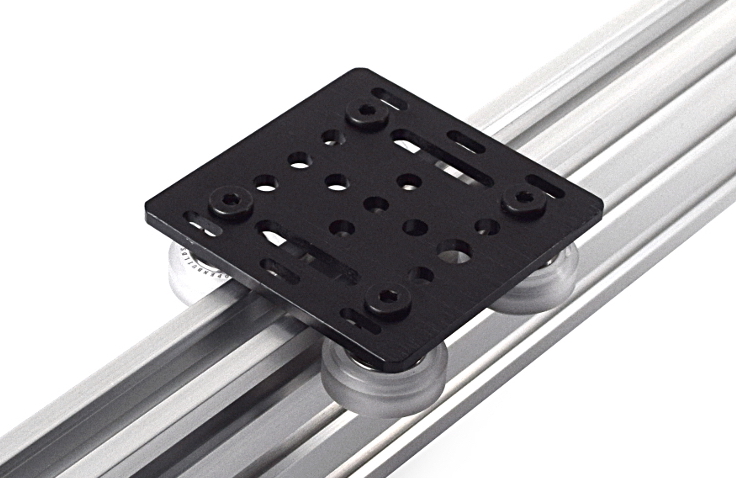
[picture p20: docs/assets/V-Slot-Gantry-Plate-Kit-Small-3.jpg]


These are really nice plates, and you could certainly make something similar out of laser-cut acrylic.

## Mounting a camera

Camera mounts are standardised around a 1/4" screw. Even mounts for phones typically have a 1/4" threaded hole so thy can be mounted on standard camera accessories, like tripods. So this is a good fitting onto which I could fit any number of off-the-shelf mounting parts, such as this [camera mount](https://www.adafruit.com/product/2464).

An aluminium baseplate could have a threaded hole to accept a 1/4" bolt. I can't create a threaded hole in an acrylic baseplate but I could create a two-layer plate, where the top layer has a hexagonal hole to capture a nut into which a bolt could be threaded.

Note: the camera needs to be able to site flush against the top face of the gantry. So any other fixings – for example the timing belt, or the bolts for the wheels – need to be recessed or otherwise out of the way. With a metal (or wooden) plate, this is easy enough, you could use countersink-headed bolts. But you can't laser-cut acrylic with countersink holes, so again, I'm leaning towards a 2-layer design. 3D printing would be another option.

## Attaching the timing belt

The Adafruit slider uses a vertical drive shaft, meaning that the timing belt is also vertical. They use a nice kinked channel in the gantry plate to hold the (continuous loop of belt) belt in place.

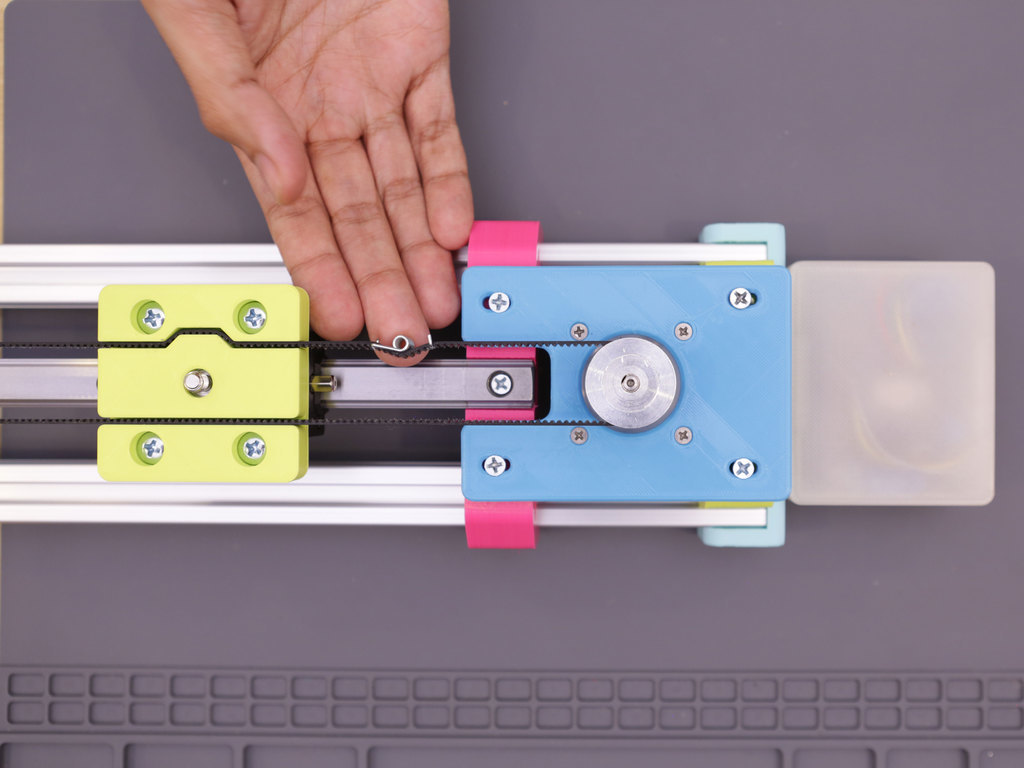
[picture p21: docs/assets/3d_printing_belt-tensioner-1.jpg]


This picture also shows the use of a belt tightener.

The Ooznest design uses a drive shaft in a horizontal orientation, so the belt is transposed through 90&deg;. You can see the slots on the edges of the gantry plate through which you could thread each end of the timing belt, to be secured with a cable grip.

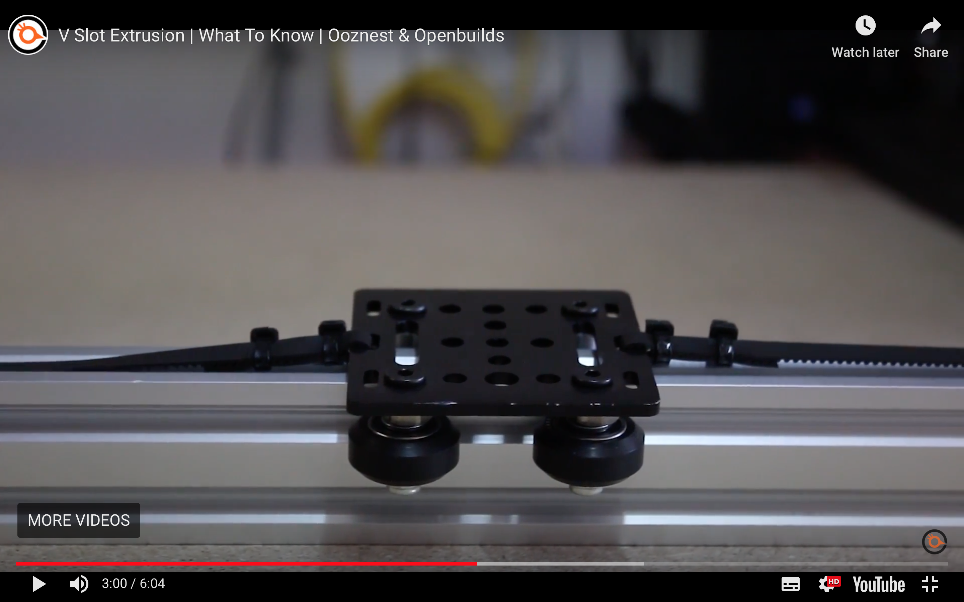
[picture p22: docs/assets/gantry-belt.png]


This approach allows you to cut the belt to whatever size works. I think this is a better approach for me, assuming I use a laser-cut gantry.

## Mounting bearings

This image of the Ooznest gantry show the kind of method I'd like to use. As they use an aluminium plate, they're able to cut recessed holes for the bolt heads to allow them to sit flush with the top surface. I think I could achieve the same effect with a 2-layer laser-cut acrylic plate. Or by conventional manual countersinking in a MDF laser-cut plate.

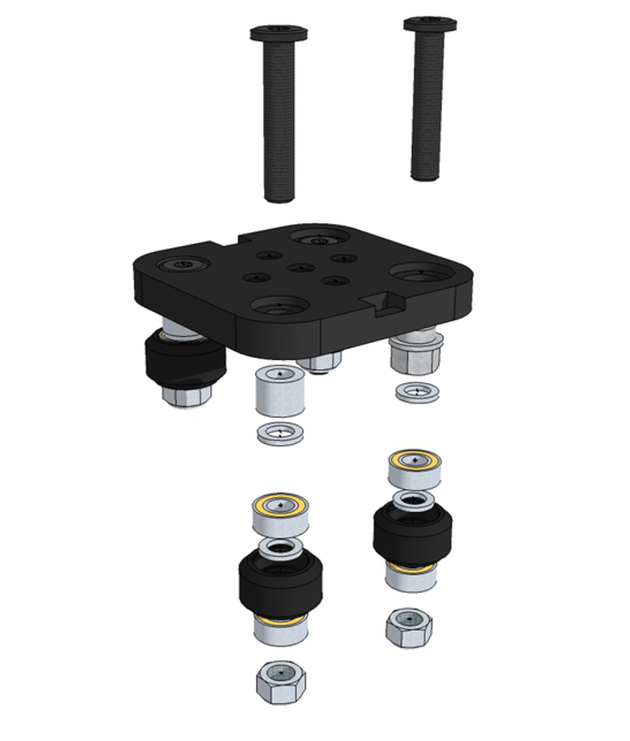
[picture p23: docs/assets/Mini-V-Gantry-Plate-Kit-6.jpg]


Some kits (e..g the Ooznest kit) use eccentric spacers to allow the wheels to be adjusted in fine increments. A simpler – and perhaps adequate – solution would be to use slots rather than round holes to accept the wheel bolts.

## Wheels/bearings

I'm looking to mount 4 wheels on bearings in a horizontal orientation underneath my gantry.
It's possible I can [3D-print the wheels](https://www.thingiverse.com/thing:1452180) themselves, but I'd still need the bearing, bolt and spacer assembly.
So I'm inclined, for version one, to buy the complete assembly, and see if I can swap out some commercial parts for DIY versions later. Apart from anything, I'd like to see what difference it makes to the motion of the gantry. But wheel kits are expensive:

* [Ooznest Delrin Dual V Wheel](https://ooznest.co.uk/product/delrin-dual-v-wheel/), including M5 bolt and 6mm spacer: £4.44 each
* [Ooznest Mini V Wheel Wheel](https://ooznest.co.uk/product/mini-v-wheel/), including M5 bolt and 6mm spacer: £3.44 each

Alternatively, cheaper versions are available on Amazon, etc. For example, [BIQU Equipment Wheel with Bearings (Pack of 5)](https://www.amazon.co.uk/BIQU-Printer-Plastic-Bearings-Passive/dp/B06X9Q9Y8V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) (£6)
 or [Samje Wheels (Pack of 5)](https://www.amazon.co.uk/Samje-Printer-Plastic-Bearings-Passive/dp/B07F61MXGR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) (£9)

## Belt

GT2 Belt seems to be pretty standard. That means it has a pitch of 2 mm between the teeth. The 6 mm wide belt seems to be the most common.

* [Ooznest](https://ooznest.co.uk/product/gt2-open-timing-belt-per-metre/): £2.90/metre
* [Adafruit](https://www.adafruit.com/product/1184): $10 / 1164mm long (continuous loop)

## Pulleys and/or bearings

I'll need at least one pulley (a toothed wheel), that can be mounted to the motor drive shaft. At the other end of the rail, I can use a bearing to allow the belt to move freely.

The image below shows the belt mechanism at one end of the Adafruit slider. Note how a smooth bearing is used, not a toothed pulley:

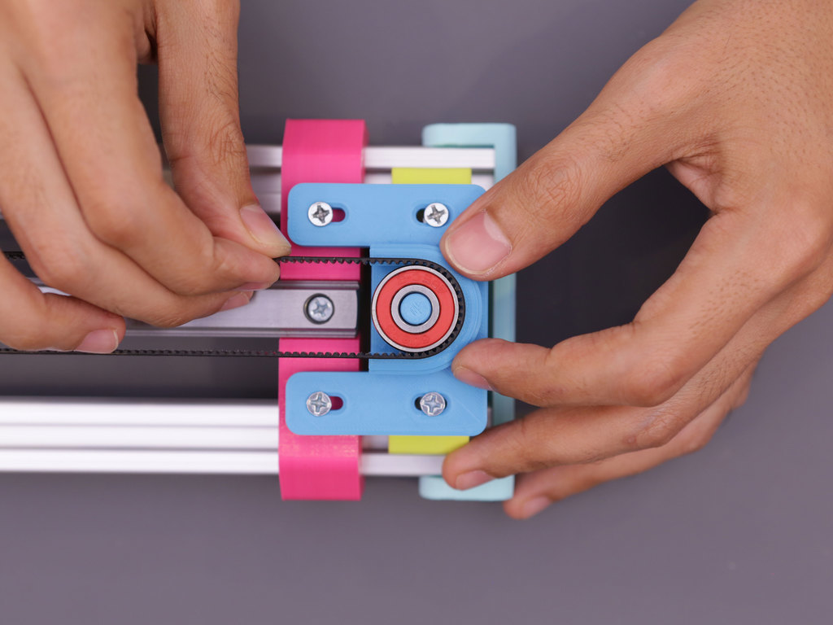
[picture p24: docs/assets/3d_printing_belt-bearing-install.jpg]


Pulleys are specified by a given number of teeth, for a certain pitch of belt. e.g. a `30 tooth GT2 pulley`. I need a 5 mm bore for the motor drive shaft, with fixing via a grub screw, and a width of 6 mm or more for the 6 mm belt.

One factor I might want to  consider here is the diameter of the pulley. [According to Ooznest](https://ooznest.co.uk/product/gt2-pulleys/), a 30 tooth **GT3** pulley (note: the description here says GT3, not GT2, but I think that may be a typo) will allow the belt to loop around both sides of a 20 mm extrusion.

I plan to run the timing belt in the cavity between two rails of aluminium extrusion, so this may not be an issue. However, if I want to include an angled rod between the two rails to pivot the gantry along its traverse, I might want to use a bigger pulley to leave some space here. The pulley and the opposite-end bearing should have roughly the same diameter.

Fortunately, [it is possible to calculate the diameter of a pulley](https://www.pfeiferindustries.com/timing-belt-pulley-pitch-diameter-outside-diameter-charts) if you know the number of teeth and the pitch.

Diameter   
= Number of teeth * Pitch / Pi  
= 30 * 2 mm / 3.14  
= 19.1 mm

For a 20 tooth pulley, this works out at 12.7 mm. Obviously this gives you the diameter on the inside of the belt, so to check for clearances, you need to allow for the thickness of the belt, and also the diameter of any fences on the pulley.

It's [possible to laser-cut pulleys](http://fab.academany.org/2018/labs/fablabbrighton/students/andrew-sleigh/assignments/2018/05/09/wk15-machine-building.html), and I think this would be an experiment worth doing, to compare with commercially made pulleys.

Pulleys:

* [Adafruit Aluminum GT2 Timing Pulley - 6mm Belt - 36 Tooth - 5mm Bore](https://www.adafruit.com/product/1253): $12
* [Ooznest GT2 Pulley 20 Tooth](https://ooznest.co.uk/product/gt2-pulleys/): £2.90
* [Ooznest GT2 (**I think**) Pulley 30 Tooth](https://ooznest.co.uk/product/gt2-pulleys/): £8.75

Bearings:

* Ooznest only sell 5 mm wide bearings. If I'm using a 6 mm belt, these won't be big enough
* [Amazon 10 x 26 x 8 mm bearings, pack of 3](https://www.amazon.co.uk/Metallic-Sealed-Groove-Bearing-6000Z/dp/B07MX91G6Q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) (£3.50)
* [RS have many 6-7 mm wide bearings at 19 mm diameter](https://uk.rs-online.com/web/c/pneumatics-hydraulics-power-transmission/power-transmission-rotary-bearings/ball-bearings/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,4294536636,4294845442&sort-by=P_breakPrice1&sort-order=asc&pn=1) (around £2 each)

You can also get 'idler pulleys', essentially a pulley mounted on a bearing, which might be a better choice for the end opposite the motor.

* Amazon: [20 teeth 5mm Bore 6mm width (Pack of 5)](https://www.amazon.co.uk/BIQU-20Teeth-Aluminum-Timing-Printer/dp/B06VSL9W9L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) (£7)

Or you can buy complete kits of belts, pulleys and idler pulleys ([This, £15 on Amazon](https://www.amazon.co.uk/KeeYees-Timing-Tensioner-Torsion-Printer/dp/B07JGXG7S2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), or [this, just the belt and 2 pulleys for £9](https://www.amazon.co.uk/JSDL-Timing-Pulley-2GT-6mm-Opening/dp/B06XQ333PN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))

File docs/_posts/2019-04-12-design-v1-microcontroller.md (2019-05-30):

---
permalink: design-v1-microcontroller/
title: Microcontroller
date: 2019-04-12
author: Andrew
layout: page
sort_id: 34
sort_tag: v1_design
---

### Microcontroller

Although I'm interested in making an integrated board that incorporates an AVR microcontroller and one or more stepper drivers, it's also a valid choice to design around a microcontroller that people already have.

For the Easy Driver-style boards, hookup varies depending on whether you want to control the microstep resolution with the Arduino (which requires 3 more pins).

The [simplest hookup](http://www.schmalzhaus.com/EasyDriver/Examples/EasyDriverExamples.html) just uses 2 pins to control step and direction, with power coming from a separate supply:

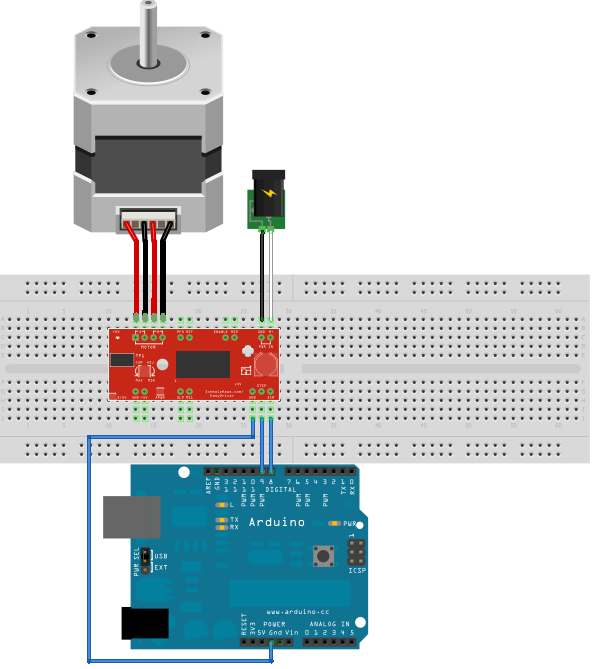
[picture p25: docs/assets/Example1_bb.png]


There is also an example given for multiple steppers, for which you need to use a library:



Again, this just uses 2 pins per motor. If I want to use two steppers, and also use all the control pins on the drivers, this may cause problems down the line...

The [Adafruit board](https://www.adafruit.com/product/1438) uses I2C, making it very easy to control multiple motors:
> Instead of using a latch and the Arduino's PWM pins, we have a fully-dedicated PWM driver chip onboard. This chip handles all the motor and speed controls over I2C. Only two data pins (SDA & SCL in addition to the power pins GND & 5V) are required to drive the multiple motors, and since it's I2C you can also connect any other I2C devices or shields to the same pins. This also makes it drop-in compatible with any Arduino, such as the Uno, Due, Leonardo and Mega R3.

Either way, for now, I should be able to get away with a standard Arduino Uno, and may be able to specify a smaller board like the Pro Mini, or maybe, for version 2, an ATtiny-based DIY board if I need only a few pins.

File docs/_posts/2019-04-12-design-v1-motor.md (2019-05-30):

---
permalink: design-v1-motor/
title: Stepper motor
date: 2019-04-12
author: Andrew
layout: page
sort_id: 32
sort_tag: v1_design
---

This project requires a stepper motor. For background on motors, see:
* [Motors – code, circuits, & construction](http://www.tigoe.com/pcomp/code/circuits/motors/)

On steppers specifically:
* [Stepper Motor Quickstart Guide - SparkFun Electronics](https://www.sparkfun.com/tutorials/400)
* [What is a Stepper Motor? -  Adafruit Learning System](https://learn.adafruit.com/all-about-stepper-motors)

Figuring out which size of motor is complicated, so instead, I went for the soft option, and asked some people who have worked with them, and looked at what other projects use. The consensus was to go for the NEMA 17. You might think NEMA is a brand name for a motor, but no, NEMA stands for [National Electrical Manufacturers Association](http://en.wikipedia.org/wiki/National_Electrical_Manufacturers_Association). The 17 refers to the size of the faceplate - 1.7" x 1.7".

According to <https://reprap.org/wiki/NEMA_Motor>
> Some (all?) NEMA 17 motors (is this specified in the standard?) have blind mounting holes 4.5 mm deep, tapped to accept M3x.50 metric bolts. The 4 mounting holes are in a square 31.0 mm (1.220 inch, about 7/32) center-to-center. The holes in the part that needs to be bolted to the NEMA 17 motor typically need to be reamed out with a 1/8" drill bit to allow the M3 bolt to pass through. The drive shaft is typically 5 mm dia.

According to <https://learn.adafruit.com/all-about-stepper-motors/types-of-steppers>:
>The NEMA numbers define standard faceplate dimensions for mounting the motor. They do not define the other characteristics of a motor. Two different NEMA 17 motors may have entirely different electrical or mechanical specifications and are not necessarily interchangeable.

Specs typically vary on a number of common parameters:
*  Number of steps per full rotation: 200 (1.8&deg; steps) or 400 (0.9&deg; steps). For time-lapse, I would assume a finer step gradation would be better. (However, most motors can also be used in a 'micro-step' mode, which breaks down these steps into 1/4, 1/8 or 1/16 micro-steps)
* Current draw (i.e. power). These vary from about 0.3A to 2A. Some motor current draws are listed as 'per phase' so I don't know how comparable these are.
* Unipolar or bipolar – from [the Adafruit guide](https://learn.adafruit.com/all-about-stepper-motors/types-of-steppers):
  * Unipolar drivers, always energize the phases in the same way. One lead, the "common" lead, will always be negative. The other lead will always be positive. Unipolar drivers can be implemented with simple transistor circuitry. The disadvantage is that there is less available torque because only half of the coils can be energized at a time.")
  * Bipolar drivers use H-bridge circuitry to actually reverse the current flow through the phases. By energizing the phases with alternating the polarity, all the coils can be put to work turning the motor.
* 2-phase or 4-phase – from [the Adafruit guide](https://learn.adafruit.com/all-about-stepper-motors/types-of-steppers):
  * A two phase bipolar motor has 2 groups of coils. A 4 phase unipolar motor has 4. A 2-phase bipolar motor will have 4 wires - 2 for each phase. Some motors come with flexible wiring that allows you to run the motor as either bipolar or unipolar.

<!-- One question for me is: what is the speed range of each motor? I'm looking for wide range of traverse speeds, from say 50 cm in 50 minutes, to 50 cm in 5 seconds. Let's see what kinds of RP ranges that would cover

Don't think this is an issue, as for slow speeds, I can just move one step at a time, with delays between -->

Lets look at some actual motors for sale:

[**Ooznest**](https://ooznest.co.uk/product/nema17-stepper-motors/)
* Bipolar
* 2-phase
* 1.33 A – 2 A per phase (but note this motor is rated at 2.8 V, so the current draw at 12 V would be different)
* 200 or 400 steps per rotation

Their cheapest motor is a 200 step 1.4 A model for £9.90 (NEMA17 Stepper Motors - 1.8° - 1701HS140A - 21oz - 1.40A)

[**Cool Components**](https://coolcomponents.co.uk/products/stepper-motor-with-cable)

This is a Sparkfun model, for about £15:

* Step Angle (degrees) :1.8
* 2 Phase
* Rated Voltage : 12 V
* Rated Current : 0.33 A
* Holding Torque : 2.3 kg*cm

[**Adafruit**](https://www.adafruit.com/product/324) seem to have something quite similar. ($14, 350 mA, 4-wire bipolar, 1.8° steps (200/revolution))

[Digikey also has some pretty similar models](https://www.digikey.co.uk/products/en/motors-solenoids-driver-boards-modules/stepper-motors/179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)

As I was buying other parts from Ooznest, I went with their 77 oz model (1.68 A/phase) for £12.65

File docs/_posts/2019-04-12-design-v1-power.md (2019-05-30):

---
permalink: design-v1-power/
title: Power supply
date: 2019-04-12
author: Andrew
layout: page
sort_id: 35
sort_tag: v1_design
---

From [Stepper Motor Quickstart Guide - SparkFun Electronics](https://www.sparkfun.com/tutorials/400):
>  Stepper motors require more power than can be supplied by the Arduino. In this example we will be powering the Uno with a 12V external supply. Notice that the power input (M+) on the EasyDriver is attached to the Vin pin on the Arduino. This will allow you to power both the Arduino and the motor with the same power supply.

From https://learn.adafruit.com/motorized-camera-slider-mk3?view=all#12v-power-14-1
> 12V Power
> To properly power the stepper motor, you need at least 12V. A USB battery pack typically is only 5V and will not provide enough juice to push the weight of a camera (be it a lightweight GoPro or Mobile Phone). I highly suggest using either a 12V power wall adapter or 12V battery pack.
> Wall Adapter
> I mostly use the camera slider indoors. Having it plugged into the wall is nice because I don't have to worry about batteries getting low and dying. This  [12V DC 1000mA power adapter](https://www.adafruit.com/product/798)  works great with this project.

The Arduino Uno has a barrel jack power input, and can pass through 12V power to the driver board, so I think this is the best way to go. I have several old 12V wall-warts that can supply 1-2 A of current.

For portable power, an [8 x AA battery power pack](https://www.adafruit.com/product/875) is probably the best option.

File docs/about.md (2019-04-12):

---
layout: page
title: About
permalink: /about/
---

These are the docs for my DIY camera slider project. 

The docs and code all live at: <https://github.com/andrewsleigh/fab-slider>

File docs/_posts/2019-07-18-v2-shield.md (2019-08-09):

---
permalink: v2-shield/
title: Designing new stepper driver and controls boards
date: 2019-07-18
author: Andrew
layout: page
sort_id: 91
sort_tag: v2_design
---

While the fundamental design (of an Arduino shield to holder the stepper driver and provide an easy way to connect controls) was sound, there were a lot of improvements I wanted to make to version 1 of the shield. These notes merge together many changes that in reality were implemented in incremental steps between v.1 and v.2.

## Board-mounted controls
In early prototypes, I tried using panel mounted controls, which would be connected by wires to headers on the board. This would enable me to assemble the case with he board inside, fit the controls to the panel , then bring the two parts together. However, I’ve never liked that approach. It’s messy, with loose wires everywhere;  introduces complexity (needing headers to connect parts); and feels like an inelegant hack.

This early prototype case shows how I thought I could mount the controls.



In contrast, many commercial products use board-mounted controls, which are either exposed directly to the user through holes in the case (like the ethernet sockets, DC socket and power switch on the left side of this circuit board from a router) or indirectly through a flexible membrane (as often seen on keypads) or a flexure in the plastic case (as in the two side-mounted buttons on the front edge of this router board)



So I decided to emulate this approach, and try to mount all the controls on the boar, and expose them through holes in the casing.

### Splitting the board into two
This introduced a new problem - the vertical space taken up by each component becomes a critical factor. I want all the exposed controls to protrude outside the case, the display to be safely inside, and all other parts to be tucked out of the way.

The driver itself is very tall: it includes a heat sink, and needs to be mounted on headers (or soldered permanently to a board). So I needed to move this to a separate board so it could be mounted out of the way. 



In this photo the boards are connected directly by headers mounted at right angles on the edge of each board. But in later versions these are connected by a ribbon cable. This board also has standard short SMD buttons, but I subsequently bought some taller buttons that are closer in height to the potentiometer.

## Simplifying  headers
Version 1 of this board is mostly just headers. I was able to simplify it greatly by changing the way I handled most of these:

### Male Arduino mounting headers
Instead or using [female ’stacking’ headers](https://www.adafruit.com/product/85)  to mount to the Arduino IO and power pins, I just used male headers mounted to the underside of the shield. The plastic frame give the shield just the right standoff to clear the USB  and power sockets. The tradeoff is that I can’t connect anything through these headers to the Arduino pins. But as I’m doing all the routing I need anyway on the shield itself, this isn’t a problem.

### Controls
I had more female headers set up to plus in LEDs, switches, potentiometers, end-stops and buttons. As noted above, I eventually decided to mount almost all of these directly for the board, so I could get rid of almost all of these (except the end-stop connection points which still still need to be exposed to a header)

### Swapping SMD for through hole 
I have access to some 10-pin female headers with SMD mounting pins. These are perfect for mounting on milled boards, as no drilling is required. But they’re expensive, and I don’t always need 10 pins on a header. The splayed feet arrangement means they also take up a lot of space on the board (J17 in the screenshot from Eagle below).

After running some tests, I was able to confirm that I can safely drill 1.1 mm holes on the milling machine, making through-hole mounting viable. 

I settled on the ‘long pads’ variant for through hole headers (J15 in the screenshot below)  to make it easier to flow solder under the headers. (It can be tricky because in most cases you’re soldering on the ‘wrong side’ of the board, and the plastic casing gets in the way)



### Connection points for motor and end-stops

The motor and the two end-stop switches are not contained within the electronics housing, so I needed to expose pins so these could be connected from outside. This photo shows those two 4-pin headers and the hole in a prototype case through which they can be accessed.



## Routing for TMC2130 stepper driver
As I’m not using the SPI functionality of this board, routing is actually easier than the A4988. Many of the pins can be left floating – i.e. unrouted. 

My board is a cheap clone of a breakout board by Watterott (which is what I would buy if I was buying another)

* Docs for the ‘SilentStepStick’ breakout board: [Pinout and Powering - SilentStepStick - Watterott electronic](https://learn.watterott.com/silentstepstick/pinconfig/)
* Docs for the TCM2130 chip: [TMC2130 - Trinamic](https://www.trinamic.com/products/integrated-circuits/details/tmc2130/)

### SilentStepStick Pinout



* EN, STEP, and DIR are routed to Arduino digital IO pins. I picked the pins to give the easiest routing when also considering the other signals that needed to go to the Arduino digital IO. All the other pins on the left side are left floating. 
* GND is routed wherever it’s needed. 
* The 4 motor pins just go straight out to the motor (via a male header)
* VMOT comes from VIN on the Arduino. And I added a capacitor here to smooth power. Power from VIN on Arduino is unregulated. 

From [In-Depth: Interface A4988 Stepper Motor Driver Module with Arduino](https://lastminuteengineers.com/a4988-stepper-motor-driver-arduino-tutorial/)
> According to datasheet, the motor supply requires appropriate decoupling capacitor close to the board, capable of sustaining 4A.
> WARNING
> This driver has low-ESR ceramic capacitors on board, which makes it vulnerable to voltage spikes. In some cases, these spikes can exceed the 35V(maximum voltage rating of A4988), potentially permanently damaging the board and even the motor.
> One way to protect the driver from such spikes is to put a large 100µF (at least 47µF) electrolytic capacitor across motor power supply pins.

See also [What Are Decoupling Capacitors in 5 Minutes](https://www.autodesk.com/products/eagle/blog/what-are-decoupling-capacitors/)

## OLED screen
I decided to add a small I2C OLED display, so I could show the selected speed, mode, direction, and any error messages. I already had 4 I2C pins exposed for this in the previous version of the board. However, they would have been connected by a cable, and I was also using the SDA and SCL pins on the Arduino Uno’s analogue IO header. The Leonardo, which is otherwise pin-compatible, doesn’t have SDA and SCL on this header, so I switched this to use the SDA and SCL pins on the digital header up by the USB port.

## Progress
This photo shows the v.1 shield on the left, and the two-part v.2 shield on the right



These board designs are all the the Git repo:
[fab-slider/boards/driver-arduino-shield/v2](https://github.com/andrewsleigh/fab-slider/tree/master/boards/driver-arduino-shield/v2)

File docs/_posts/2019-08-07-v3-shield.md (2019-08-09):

---
permalink: v3-shield/
title: Designing a new board — again
date: 2019-08-07
author: Andrew
layout: page
sort_id: 92
sort_tag: v2_design
---

My [previous 2-board design](../v2-shield) worked OK, but I struggled to find a way to enclose it in a reasonably-sized case.

I made two changes that enabled me to move on to a more compact design:

1. I ditched the Uno form-factor, and swapped it for an Arduino Nano. These are cheap enough that they can be embedded permanently in the project, can draw power from the same 12 V supply that the motor needs, and are a quarter of the size of an Uno.

2. I realised the mix of SMD and through-hole components could work in my favour. All the controls (except the OLED screen) are surface-mount, and should be soldered directly onto the front copper face of the board. But the Arduino Nano, the driver shield and the connections to the motor and end-stops are all just headers, which are more readily available in through hole versions, and are much easier to solder from behind.

So I was able to make effectively a two-sided board, while still only needing to mill the copper on one side.

The front (copper side) of the board, with all traces and user-facing components:



You can see here I also made a simple mount for the OLED screen, to hold it square on the board.

The back side of the board, which just has female headers for the Nano and driver module, and male headers for connections to the motor and end stops:



(Not visible here is the smoothing capacitor underneath the driver module.)

<!-- ![IMG_2599.jpg]({{ "/assets/IMG_2599.jpg" | relative_url }}) -->

This board is still quite bulky, largely because of the driver heatsink, but I was able to make the footprint small enough that it could be mounted on the end of the slider frame, which is 80 mm wide.



There are a couple of improvements I'd like to make:
* Flip the Nano around so its USB port is accessible without removing the board from the faceplate.
* Use the through-hole DC jack mounted to the underside of the board so no cutout is needed on the faceplate.
* Use straight instead of right-angle headers for the external connections to the motor and end-stops. I chose these because I was going to put this board inside a case, but mounted this way, it would make more sense if they just went straight down from the board.

These board designs are all the the Git repo:
[fab-slider/boards/driver-arduino-shield/v3](https://github.com/andrewsleigh/fab-slider/tree/master/boards/driver-arduino-shield/v3)

As is an STL for the  OLED display mount:
[fab-slider/3d-parts/v1/electronics-face-plate](https://github.com/andrewsleigh/fab-slider/tree/master/3d-parts/v1/electronics-face-plate)

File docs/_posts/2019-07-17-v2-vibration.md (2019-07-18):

---
permalink: v2-vibration/
title: Addressing vibration with a different stepper driver
date: 2019-07-17
author: Andrew
layout: page
sort_id: 81
sort_tag: v2_design
---

My biggest problem with version 1 was the vibration coming from the stepper motor, and being transferred through the drivetrain to the camera. With modern iPhones’ non-optional optical image stabilisation, I was getting vary bad results from the small – but very inorganic – vibration motion.

I figured there were three avenues I could explore:

* Using a brushed DC motor instead of a stepper
* Mechanical fixes
* Using a different stepper driver

## Experimenting with DC motors

I thought this might be an option, as one of the commercial sliders I’m aware of uses a DC motor:
[Ratrig V-Slider DIY Camera Slider kit](https://ooznest.co.uk/product/v-slider-diy-camera-slider/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) 

I didn’t go to far down this path as I didn’t want to shell out for a new DC motor, and the ones I had to hand weren’t ideally geared for this job.

I did manage to blow my Arduino trying to drive a DC motor directly, so I ordered a replacement and a L298N driver and had some limited success following this guide: [Arduino DC Motor Control Tutorial - L298N - PWM - H-Bridge - HowToMechatronics](https://howtomechatronics.com/tutorials/arduino/arduino-dc-motor-control-tutorial-l298n-pwm-h-bridge/).

However, with the motors I had to hand, there was too much whining. I’m guessing this is probably because they expect a 24 V supply, but all I have to hand is 12 V.

## Mechanical fixes
I haven’t tried any of these out yet, but some digging turned up a few ideas of things to try:

From [How do you minimize stepper motor vibration? - Electrical Engineering Stack Exchange](https://electronics.stackexchange.com/questions/11811/how-do-you-minimize-stepper-motor-vibration):

> … fundamentals of eliminating resonance and buzzing in mechanical subsystems is raise the resonant frequency with a stiff chassis and decouple with elastomer shock mounts to attenuate structure resonance or if not possible, then add viscous dampening.

And:

> In my research, I came across a belt tensioner (spring loads belt) to help dampen the step pulse. If you are using a belt this could help.
> To reduce vibration:
> 1 add mass - such as a flywheel, etc.
> 2 insulate - use third party to deliver power
> 3 reduce force - lower current, microstep or (In my case add a spring belt tensioner) many others ways to reduce force.
> 4 tuning - run motor at higher speeds with reduction if applicable
> 5 dampen - such as a “shock absorber”, could be like a spring belt tensioner with shock

From [How to Take Vibration out of Stepmotors - Machine Design](https://www.machinedesign.com/motorsdrives/how-take-vibration-out-stepmotors):

> Shift the resonance frequency by changing current or voltage, inertial load, or step resolution.

From [Stepper motor vibration/resonance etc..how to elliminate?](https://www.cnczone.com/forums/stepper-motors-drives/111911-stepper-motor-vibration-resonance-etc-elliminate.html):

> It might be necessary to fill the alloy sections with some dampening material with a high modulus such as stiff silicon rubber or an epoxy cement based material, Adding webs would also raise the stiffness and hence reduce any mechanical resonance in the axis track. 

## Using a different stepper driver
So far, this is the route I’ve pursued the furthest. 

### DRV8825

This is a common alternative to the A4988. The breakout boards are pretty much pin-compatible, and it offers one more level of micro-stepping: down to 1/32 step. I didn’t choose this driver as there was a better alternative, but I did find some useful resources:

General information: [Pololu - DRV8825 Stepper Motor Driver Carrier, High Current](https://www.pololu.com/product/2133)  

Comparison to older A4988: [A4988 vs DRV8825 Chinese Stepper Driver Boards - RepRap](https://reprap.org/wiki/A4988_vs_DRV8825_Chinese_Stepper_Driver_Boards)  

DRV8825 Pinout: [In-Depth: Interface DRV8825 Stepper Motor Driver Module with Arduino](https://lastminuteengineers.com/drv8825-stepper-motor-driver-arduino-tutorial/#microstep-selection-pins)  



Compared to A4988 Pinout: [In-Depth: Interface A4988 Stepper Motor Driver Module with Arduino](https://lastminuteengineers.com/a4988-stepper-motor-driver-arduino-tutorial/)  



### TMC2130

This driver was recommended to me by Ooznest. It has a load of nice features for more advanced stepper control, but the chief benefit of interest to me is **1/256 resolution** micro stepping. Which they call “stealthChop”… 

From the datasheet (p39):
> stealthChop is an extremely quiet mode of operation for stepper motors. It is based on a voltage mode PWM. In case of standstill and at low velocities, the motor is absolutely noiseless. Thus, stealthChop operated stepper motor applications are very suitable for indoor or home use. The motor operates absolutely free of vibration at low velocities. With stealthChop, the motor current is applied by driving a certain effective voltage into 
> the coil, using a voltage mode PWM. There are no more configurations required except for the PWM voltage regulator response to a change of motor current. Two algorithms are provided, a manual and an automatic mode. 

The driver can be controlled over SPI, or by pulling config pins high or low. For the basic features I need, SPI is overkill, and in fact, I can leave most of the configuration pins floating and it defaults to the setup I need.

SPI mode is set by soldering (or desoldering a jumper on the board. The default state for this jumper is different on different boards. I have a particularly poor version, the BIGTREETECH
TMC2130-V1.1. However, there is a [manual](https://github.com/bigtreetech/BIGTREETECH-TMC2130-V1.1), in Chinese, which says:

> Q:驱动选择了 SPI 模式，但又想用回 STP/DIR 工作模式，怎么 办?  
> A:将 CFG4 和 CFG5 的连接断开，再把 R5 的两个焊盘连接起 来，如下图红色部分需要焊接，红框内不连接 

Translated:

> Q: The driver selected the SPI mode, but want to use the STP/DIR working mode. What should I do?  
> A: Disconnect the CFG4 and CFG5, and connect the two pads of R5. The red part of the figure below needs to be soldered, and the red frame is not connected

This is in fact how the module comes, so no soldering is needed on these tiny pads. 

There is an explanation of how to use the config pins (when not using SPI mode) in the TMC2130  datasheet:

> **24 Standalone Operation**
> For standalone operation, no SPI interface is required to configure the TMC2130. All pins with suffix CFG0 to CFG6 have a special meaning in this mode. They are evaluated using tristate detection, in order to differentiate between 
> CFG pin tied to GND
> CFG pin open (no connection) 
> CFG pin tied to VCC_IO 



I also found this  video helpful:
[TMC 2130 Stepper Drivers - Standalone Mode - Chris’s Basement - YouTube](https://www.youtube.com/watch?v=Jh8iwqc1TP0)

The upshot is that I was able to design a new driver shield board with very minimal changes to accommodate the different pinout of this driver. These changes are described on the page for the new shield design.

So far, the results have been very good.

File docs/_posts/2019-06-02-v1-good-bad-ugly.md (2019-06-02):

---
permalink: v1-good-bad-ugly/
title: Version 1 – The good, the bad and the ugly
date: 2019-06-02
author: Andrew
layout: page
sort_id: 71
sort_tag: v1_review
---

Slider hero shot

I’ve got to a pretty good place with version 1 of my slider. I have a functioning product, that does pretty much what I set out to do (with one big caveat - see below). And I also have a long list of improvements I’d like to make for version 2. So now’s a good time to draw a line under version 1, and reflect on the process and results.

<iframe width="560" height="315" src="https://www.youtube.com/embed/r8nMpmrksCw" frameborder="0" allow="accelerometer; autoplay; encrypted-media; gyroscope; picture-in-picture" allowfullscreen></iframe>

<!-- 
![]({{site.baseurl}}/assets/)
![]({{site.baseurl}}/assets/)
 -->

## The good

### Learning about 3D printing and driving motors

A lot of the good things are about the process more than the machine itself. Two things I wanted to explore more, and I really enjoyed it. I loved designing the 3D parts, and spending more time in Fusion 360. This is becoming more of a creative environment fr me know, and less of a chore. The Creality CR10 printer I used was great. A real workhorse, and most things pretty much ‘just worked’.

Printing a bracket

Stepper motors were a big grey cloud of uncertainty when I started. I didn’t really know how they worked, how to choose one, or how to drive it. Now I’m much more confident in this area. One thing I’ve seen on the horizon, but not touched yet, is [Grbl](https://github.com/grbl/grbl/wiki). I’d like to find an excuse to look into this some more.

### Doing more with Arduino, state machines

My Arduino skills are slowly bedding in. I did a lot of research into state machines, and found this model to be immensely helpful, even though I ended up simplifying my state machine drastically from the original idea.  

### Documentation

I’ve written *a lot* of documentation for this project! Maybe even too much. But I think the process has helped me be more systematic and rigorous in my work.

### Arduino Shield

Stepper driver, shield and Arduino

Like Fusion 360, Eagle is frustrating software for the uninitiated. But as I get more comfortable with it, I find it very rewarding. I’m quite pleased with my simple driver shield, and think it supports the project aims of being easily replicated by others. 

### Architecture

I settled on this architecture:
* Widely available commodity machine parts (aluminium extrusion, M5 fixings)
* Commodity motor control electronics (cheap A4988 stepper driver boards)
* Stock Arduino Uno microcontroller
* Easily fab-able parts: driver Arduino shield, 3D-printed gantry and brackets, laser-cut end caps 

I think this strikes a good balance between building everything yourself, and making use of affordable manufactured parts. It’s not simply piecing together a kit, nor is it DIY as a form of punishment. There are plenty of opportunities for learning, and for optimisation in design and making, and by version 2, I think I will be able to make a well-integrated product that could feasibly by used in a production environment. 

There are other ways of doing the electronics for this project, but I think the approach of Arduino Uno + DIY shield + cheap commercial driver board allows for a good mix of replicability, cost-effectiveness and accessibility.

### Potential student project

I think this could be a great student project, with plenty of room to learn about motion control, machine building, software, assembly, materials, and perhaps most importantly, quality,  which I’ll come back to later. 

As a challenge for students, it could also be generalised slightly to be a ‘one-axis CNC machine’, which would allow for lots of interpretations (from a drawing robot to a drinks dispenser) so students could make something that really appealed to them.

## The bad

### Integration

Not integrated electronics

The electronics are still loose, with a breadboard, jumper wires and other bits and pieces all dangling precariously. Clearly this needs a case. Once I’ve enabled the motor issues, this will be a key part of the version 2 build.

### Driver shield improvements

I’ve already designed a much better Arduino shield to hold the stepper driver board. That would be a straight drop-in replacement for the one I’m using now. However, I’m putting this on hold until I’ve decided what motor and driver combination to use for version 2.

### Construction dependencies

I need to do some more experiments with different kinds of V-slot fixings. Threaded holes in the ends are the most mechanically sound, but unless you’ve got good quality taps and you know how to use them, it’s easy to mess up tapping holes. Many machines like this rely on right angle brackets, specialised v-slot nuts or 3D-printed mounts that mate with the v-slot profile. 

This needs more experimentation, but I’d like o find a way to build this without depending on threaded holes in the ends of the extrusion.

### Industrial design niggles

I noticed a few problems with the industrial design and construction, which I’ll need to look at workarounds for:

* The right-angle brackets at the read end coming loose 
* The idler pulley interferes with the rear end cap
* The bolts securing the camera D-ring capture plate from underneath interfere with the timing belt
* The end-stop switches are difficult to mount: there is no easy way to access the fixing bolt once the bracket is on the rail
* The gantry currently has two bolts designed to hit the end-stop switches at the end of the traverse. I ghoul die able to get away with one.

### Melting PLA

Warped PLA gantry

I’m currently in a hot climate (daytime temperatures up to 35 °C) and that seems to have partially melted one of my PLA parts. As far as I understand, [PLA shouldn’t start to become plastic until about 60 °C](https://reprap.org/wiki/PLA), so I’m not quite sure how this happened. Nevertheless, I may need to look at alternatives: either printing in ABS, or avoiding 3D printed parts altogether (I was able to replace the gantry with an alternative 2-part glued version I laser-cut from MDF).

### In use

This version is designed to sit on a table with the camera directed out from the slider, also horizontally. By using an adjustable tripod mount, you can also have it point slightly up, down or whatever. However,  I soon found that a very useful orientation for filming is top-down. For example, mounting the slider above a work area filming a process from above. There’s no easy way to do this with the current design.

In this use case, having a way to position the slider on its side, or mount it on a vertical surface would be useful.

When using it outside, flat, horizontal surfaces are hard to come by. So here, adjustable feet or a tripod mount would also be good features. Although I’m skeptical about how stable something this heavy would be on a tripod. Even just more widely-spaced feet would help. 

And something which I considered at the beginning – but which I never intended to put in version 1 – is some form of target tracking, even just an approximate angling of the camera towards the centre point as it makes its traverse.

## The ugly: vibration

I had always been concerned about vibration form the stepper motor. I’m using 1/16th micro stepping to limit this, but even in this mode, there is considerable visible camera shake caused by vibration in the system.

For m, this is a question of *quality*. As a DIY maker project, it’s about 90% there. But that last 10% is just as important. And likely just as difficult. But I don’t want to make an OK slider; I want to make a really good one.

After doing many tests, I’ve identified a number of factors which seem to contribute, aside from the vibration from the stepper motor. In particular, anything which causes camera instability regardless of whether the motor is running:
* Wind, when using outside
* Filming with a phone mounted in a phone tripod mount, instead of a heavy, flat-bottomed SLR-style camera mounted straight to the gantry
* Adding an adjustable tripod adapter to enable positioning, which amplifies any motion   

But the killer is automatic optical image stabilisation (OIS), which at least on my phone, can’t be switched off. I was able to test the slider with an iPhone XR (automatic-OIS) and an iPhone 6s (no OIS) and the difference is remarkable:

<iframe width="560" height="315" src="https://www.youtube.com/embed/-GZw0JKbzWQ" frameborder="0" allow="accelerometer; autoplay; encrypted-media; gyroscope; picture-in-picture" allowfullscreen></iframe>

Clearly the OIS system is really thrown off-kilter by the vibrations from the motor. However, even the non-stabilised footage form the 6S is too shaky to make the grade. It’s not so noticeable when shooting time-lapses, although again, using the iPhone’s built-in time-lapse camera mode, the OIS effect is pretty bad. 

It’s much better with a real camera, but I want this machine to be usable with a phone. So this is something I need to address.

### Options

I might be able to get one more level of Microstepping (down to 1/32 of a step) by using a different driver (a DRV8825 instead of an A4988). I’m looking into this:

[Stepper Driver Noise: A4988 vs DRV8825 (Updated) - YouTube](https://www.youtube.com/watch?v=tGd2ulVkDTM)

I’m also researching DC motors, which might be more suitable than the stepper I’m currently using. 

There might also be mounting or construction techniques I can use that will minimise vibration throughout the system, and in particular stop It being amplified by the time it gets to the camera.

## Wishlist for version 2

So that leaves with a nice list of things to try for my next version:

* A different motor, or a way of driving the stepper with less vibration
* Design and construction for damping of vibrations
* Different mounting options: tripod, on its side, attached to a vertical surface
* Integrated housing and tidy internal cabling for all parts: no breadboards or loose jumper wires
* Industrial design that doesn’t require tapped holes in the extrusion
* Better feet for stability outside in wind or on uneven surfaces
* ABS printing of plastic parts
* Improvements to the pulley and end-stop mounting, and gantry end-stop bolts
* A revised driver shield board

And some things that I might bump to version 3, if I get that far:

* A smaller version, maybe using a smaller motor and only one rail, to reduce material usage, cost, size and weight (perhaps one that could be powered from a 5 V USB power supply, or 3.7 V LiIon/LiPo battery for portable use)
* Wireless control over bluetooth or wifi via a smartphone app (of course, ideally this would integrate control of the camera on the phone as well!)
* A simple GUI on an OLED screen to show basic parameters such as speed, mode and direction

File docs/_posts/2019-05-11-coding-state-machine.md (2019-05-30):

---
permalink: coding-state-machine/
title: Building a state machine
date: 2019-05-11
author: Andrew
layout: page
sort_id: 51
sort_tag: v1_code
---

In my [last significant Arduino project](http://fab.academany.org/2018/labs/fablabbrighton/students/andrew-sleigh/final-project/), I came across the concept of a state machine. I didn’t have time to look into it then, but when I started to think about the software for this slider, it came to mind again, and I decided to investigate.

## What is a state machine?
Paraphrasing from [Wikipedia](https://en.wikipedia.org/wiki/Finite-state_machine):

> A system that can be in exactly one of a finite number of states at any given time. The state machine can change from one state to another in response to some external inputs; the change from one state to another is called a transition. A state machine is defined by a list of its states, and the conditions for each transition. 

When we’re thinking about useful machines – things that do something, this minimal definition could be expanded a little. Specifically, in each state, there is some sort of output: a light flashes, a motor turns, or an error message is logged. Here’s a description with more of a hardware focus, from [State Machines and Arduino Implementation](https://www.norwegiancreations.com/2017/03/state-machines-and-arduino-implementation/):

> **States**  
> An embedded system should at any given time be in a defined state, whether it is “moving left”, “door open”, “stopped”, “init”, “error” or any other imaginable state. The states and the transitions between them make up the main structure of the state machine.
> 
> **Inputs**  
> Inputs are what makes the system switch states and can for instance be switches, buttons and sensors or any other typical embedded input.
> 
> **Outputs**  
> Outputs in a state machine can be motor movement, lights or any other typical embedded output.

## Why is it useful?
I was initially drawn to state machines because it seemed like a natural model for my slider: it’s always going to be in one of a number of states: calibrating itself, waiting start a traverse, doing the actual traverse, stopping in case of an error, etc. 

However, I quickly realised there are a couple of related benefits.

### Simplifies event handling

From [UML state machine - Wikipedia](https://en.wikipedia.org/wiki/UML_state_machine):

> The concept of a FSM is important in  [event-driven programming](https://en.wikipedia.org/wiki/Event-driven_programming)  because it makes the event handling explicitly dependent on both the event-type and on the state of the system. When used correctly, a state machine can drastically cut down the number of execution paths through the code, simplify the conditions tested at each branching point, and simplify the switching between different modes of execution. Conversely, using event-driven programming without an underlying FSM model can lead programmers to produce error prone, difficult to extend and excessively complex application code.

For me, this is huge. I have to consider so many possible inputs, especially when looking at all the ways the slider might go wrong. So if I can isolate its behaviour into a set of discrete states, I can simplify the inputs I need to worry about. e.g. I don’t need to worry about changes to the speed control whilst calibrating; I don’t need to poll the end-stop switches while the slider is stationary.

### Forces you to solve most problems before writing any code

You can’t build a state machine without a clear model of the states, inputs, transitions, and outputs. This model is usually drawn as a *state machine diagram*.  As soon as you get into writing code, and testing it with hardware, many tings can go wrong, and it’s difficult to see sometimes whether the problem is in the system you’re making, the logic of the code, or you’ve just left a semi-colon off the end of a line, or forgotten to connect a button to ground. 

As I was drawing my state machine diagram, I found that I had to think about all of the error handling, the user interface, and flow of actions before writing any code. And I solved almost all the hard problems in the course of drawing the diagram. I think if I’d dived straight into code, I would have been in a tangled mess very soon. 

## Drawing a state machine diagram
I used the excellent Omnigraffle software to draw my diagrams. Note that these are [not flow charts](https://en.wikipedia.org/wiki/State_diagram#State_diagrams_versus_flowcharts). There are several resources  (see below) that go into lots of detail about how to draw a syntactically correct diagram, even [some dedicated modelling software](http://staruml.io), but I was mostly concerned with getting the basics right, capturing:
* All possible states
* All relevant  events that could happen in each state and what transitions these would trigger to other states

Here was my first rough attempt:



After several hours work, I ended up with something more comprehensive, and with an alarming number of arrows. 



In this diagram, each circle is a state, and each arrow is a transition. The flow is pretty linear, going from top to bottom one state after the next, and the only deviation from the path coming if there is an error (typically the slider hitting an end-stop when we’re not expecting it), or the user pauses or cancels an operation. 

So while it might look complex, in fact it captures all the functionality I need to build (mostly things that are done in the green circles: such as calibrating the ends of the slider) and the inputs I need to listen for – and critically when I do and don’t need to listen for them. This made coding even  this complex machine way easier. 

After building most of this, and then testing with my prototype hardware, I realised a major flaw in my design. In this model, a key step is calibration. After starting up, the slider moves to each end of the rail, until it hits each end-stop, to get the position data for each end. It then uses this to move to one end (depending on the direction the user sets), and also to perform the actual traverse to the other end (so it knows how fast to go for a given duration, and also when to stop).

Once it’s calibrated, the motor must remain powered to keep the spindle locked in the same position. If the user were to move the gantry by hand after calibration, all of that data would become incorrect. That draws power, and also creates noise, so I wanted to include transitions so it could timeout back to a startup position after a while, or the user could reset it by hand.

### Simplifying

The calibration process (and these extra events) added complexity and  time to the process, and I soon got bored of going through all these steps when testing my code. So I wondered if I could simplify things. What would happen if I just ditched the calibration process, and worked on the assumption that the slider never knew where it was, or (until it hit a stop switch) where the ends were? 

Sure enough, as I removed this state from the machine, other states also became redundant, and my next version was drastically simpler:



With no calibration step, the slider is ready to accept input as soon as it’s switched on. Rather than moving from one end all the way to the other, in the direction the user specifies, it just moves in that direction from wherever it happens to be at that point, and stops when it hits an end stop. No data about current location or the position of end-stops needs to be retained, so the motor can be switched off whenever it’s stationary. There’s no need for timeouts, manual resets or soft pausing (remembering this data for when the pause is released).

I’d written all the code for the complex version by the time I figured this out. However, it was a useful lesson in complexity: as you add states to a state machine, complexity increases non-linearly; and can quickly get out of hand. I was also able to dig deeper into the stepper library I’m using. And it was kind of cool watching the machine calibrate itself; so I’m kind of sad to see that go.

I’ve posted the old – complex – code in the repo in case anyone’s interested: [fab-slider/arduino-code/old-complex-state-machine at master · andrewsleigh/fab-slider · GitHub](https://github.com/andrewsleigh/fab-slider/tree/master/arduino-code/old-complex-state-machine)

## Scaffolding in code
The code to handle this in Arduino is very simple. First, set up an `enum` to hold all your possible states:

```
enum possibleStates {
  INIT,
  TRAVERSING,
  ABORT
};
```

Then create a variable of this type to track the current state:

```
enum possibleStates currentState;
```

Then in your main `loop()` function, use a `switch` statement to control flow through the states:

```
switch (currentState) {
  case INIT:
    // do stuff you need to do on startup
    // e.g. switch the motor off, get inputs for direction, speed, etc.
    
    break;

  case TRAVERSING:
    // move the slider with whatever parameters the user set
    // don't get any more inputs from user controls
    // stop and pull back when you hit an end stop

    break;

  case ABORT:
    // stop the motor, print error messages

    break;
}
```

## Further reading

These are some resources I found helpful

**On state machine theory**

* Modeling Software with Finite State Machines (book)
* [A State Machine Crash Course](https://docs.spring.io/autorepo/docs/spring-statemachine/current-SNAPSHOT/reference/#crashcourse)

**On diagrams**

* [State diagram - Wikipedia](https://en.wikipedia.org/wiki/State_diagram)
* [UML state machine - Wikipedia](https://en.wikipedia.org/wiki/UML_state_machine)
* [StarUML documentation: Statechart Diagram](https://docs.staruml.io/working-with-diagrams/statechart-diagram)
* [UML State Machine Diagrams - Overview of Graphical Notation](https://www.uml-diagrams.org/state-machine-diagrams.html)

**On state machines in Arduino**

* [Microcontroller state machine with enum tutorial](https://www.baldengineer.com/state-machine-with-enum-tutorial.html)
* [Finite State Machine on an Arduino: 7 Steps](https://www.instructables.com/id/Finite-State-Machine-on-an-Arduino/)

## Next steps

Some other things I want to talk about soon:

* [Understanding the AccelStepper library](../coding-accelstepper/)
* [Building a better debugging system using the Arduino serial monitor](../coding-better-debugging/)

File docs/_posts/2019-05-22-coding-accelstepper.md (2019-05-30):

---
permalink: coding-accelstepper/
title: Understanding the AccelStepper library
date: 2019-05-22
author: Andrew
layout: page
sort_id: 53
sort_tag: v1_code
---

I decided to use the AccelStepper library to handle motion control for this project. As my state machine became simpler, I suspect the need for this became less urgent, and I could have made do with the standard Arduino stepper library, or even just written some functions myself to control the motor directly by pulsing the step pin.  

However, I spent some time getting to grips with this library, so I wanted to record a few things I learned here, not least because the library comes with sparse examples, and minimal documentation generated with the docs builder [Doxygen](http://www.doxygen.nl/index.html), which I find to be pretty unhelpful. Critically, I can't find anywhere a description of the conceptual model AccelStepper uses. What does it mean by 'move' or 'run' or 'stop', and how do these concepts relate to each other? These are things that I guess it's easy for an experienced user to understand, but opaque for a new user.

As I'm in the middle of learning this stuff, I feel readers should exercise particular caution here: there could be many mistakes, misunderstandings or poor recommendations ahead. Proceed with caution!

## Creating a stepper object with the constructor function.

Docs here: <https://www.airspayce.com/mikem/arduino/AccelStepper/classAccelStepper.html#a3bc75bd6571b98a6177838ca81ac39ab>

Initially I was confused by the `FULL4WIRE` and `FULL2WIRE` options. My motor has four wires, so that seemed appropriate, but then it is controlled with 2 pins, so that could also be correct. Eventually, I realised that because I'm using an A4988 driver, I should use the `DRIVER` option. And because my shield has DIRECTION on D3 and STEP on D2, I should specify those arguments like so in the constructor:

```
AccelStepper stepper(AccelStepper::DRIVER, 2, 3);
```

Possibly a case of RTFM... 

## Moving from one known position to another known position

This is the most basic functionality I needed to enable (when I was using calibrated end positions). It gives some idea of how the different library concepts can work together:

```
stepper.moveTo(rightEndStopPosition); 
stepper.setSpeed(traverseSpeed); 

while (stepper.currentPosition() != stepper.targetPosition()) { 
  stepper.runSpeedToPosition();
}
```

In this simplified code (the full code is in [traverse.ino](https://github.com/andrewsleigh/fab-slider/blob/master/arduino-code/old-complex-state-machine/State_Machine_6/traverse.ino), the gantry moves from the left end to the right at a constant speed. You can see how the function `moveTo()` doesn't actually move anything. It took me a while to figure that out.

## Getting an end-stop position.

Useful if you want to calibrate the slider so you know where the two ends are:

```
if (digitalRead(leftEndStopPin) == HIGH) { // if it touches an end-stop 
  leftEndStopPosition = stepper.currentPosition(); 
  gotLeftLimit = true; // a boolean variable for tracking calibration status
  stepper.stop(); 
  stepper.runToPosition(); 
}
```

Note that `stop()` doesn't stop the motor! It just sets a new target at the current position. You then need to `runToPosition()` to actually stop the motor.

## Blocking and non-blocking functions

Because I want the user to be able to pause or cancel a slide, and also for the end-stops to be able to halt movement, I can't have the stepper control functions block other inputs. Generally, it seems (and I might be wrong) that library functions that implement acceleration are blocking, those that don't aren't... 

## Using acceleration

I think this is the raison d'etre of this library. I think it could be useful for me in two scenarios:

1. Giving more naturalistic slides in video mode by easing in at the beginning and easing out at the end of the traverse
2. Moving heavy loads (like a DSLR camera) with more stability and les risk of motor slippage by avoiding sudden starts and stops

Some of the library functions implement acceleration (e.g. `runToPosition()`), and some don't (e.g. `runSpeedToPosition()`). 

I believe that the program needs to know the total number of steps in a given traverse so that it can calculate how fast to accelerate/decelerate, and when to start decelerating. So in my original version of the code, in which the end positions were calibrated, I could use this everywhere. But in my new simpler version, the program can't know how how many total steps there are in a traverse, so I only use acceleration in the small backing-off movements when the gantry hits an end-stop and I want it to back off the switch lever:

```
stepper.runToNewPosition(leftEndStopPosition+endStopPadding);
```

This is a blocking function, but that's not a problem in this particular situation.

I need to do some more tests in the two scenarios noted above. I may need to do some more work in my code to implement acceleration and deceleration. <span class="wip">WIP</span>

## Disabling the motor

I don't want to keep the motor powered when I'm not moving the slider. It uses power and makes an annoying noise. The library has a [function](https://www.airspayce.com/mikem/arduino/AccelStepper/classAccelStepper.html#a3591e29a236e2935afd7f64ff6c22006) `disableOutputs()` which might do what I want, but I couldn't figure out how to get it to work. So instead, I just connected the ENABLE pin on my driver to one of the Arduino's digital outputs and pulled it high to disable the motor:

```
digitalWrite(motorOffPin, HIGH);
```

From the datasheet:

> Enable Input
> This input turns on or off all of the FET outputs. When set to a logic high, the outputs are disabled. When set to a logic low, the internal control enables the outputs as required. The translator inputs STEP, DIR, and MSx, as well as the internal sequencing logic, all remain active, independent of the ENABLE input state.

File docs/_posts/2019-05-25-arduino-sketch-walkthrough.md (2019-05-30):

---
permalink: arduino-sketch-walkthrough/
title: Walkthrough of the Arduino sketch
date: 2019-05-25
author: Andrew
layout: page
sort_id: 64
sort_tag: v1_code
---

I've got the Arduino code to the stage where it's good enough for the version 1 machine. There's a lot I'd like to change for the next version, though mostly on the hardware side, but here seems like a good place to take and share a snapshot.

This post is just is a lightly documented version of the code for the first version of my camera slider. This is much simplified from the [old complex state machine](../coding-state-machine/). Here's a diagram of the simpler state machine I'm building in this code:



All the code is here:
<https://github.com/andrewsleigh/fab-slider/tree/master/arduino-code/v1>

## Libraries

I'm using these Arduino libraries to handle motor control, non-blocking timers, and button debouncing respectively:
```
#include <AccelStepper.h>
#include <neotimer.h>
#include <Bounce2.h>
```

## User configuration

The variables that you might want to change are listed at the top of the file so speeds can be tweaked

```
int videoMinSpeed = 500;
int videoMaxSpeed = 5000;
int timelapseMinSpeed = 50;
int timelapseMaxSpeed = 250;
int endStopPadding = 100; 
```

## Debugging setup

As documented in [Better debugging with the serial monitor](https://andrewsleigh.com/fab-slider/coding-better-debugging/) (or [GitHub link](https://github.com/andrewsleigh/fab-slider/blob/master/docs/_posts/2019-05-12-coding-better-debugging.md)), this section sets up the definitions that allow you to switch serial debugging on and off. You'd want to turn it off in use because sending all that data to the serial monitor interrupts the motion of the stepper.
```
String errorMessage = ""; // this string needs to be initialised even if we're not running debugging

// comment these out to remove debugging
#define DEBUG // needed for all debugging
// #define DEBUG_TIMER // for messages that print every few seconds
// #define DEBUG_STATE_CHANGE // for messages that print only on a change in the machine state

#ifdef DEBUG

// set up string messages
#define DEBUG_PRINT(str)    \
  Serial.print(str); \
  Serial.print(" ------ ");      \
  Serial.print("In ");    \
  Serial.print(__PRETTY_FUNCTION__); \
  Serial.print(", line: ");      \
  Serial.println(__LINE__);     \

#else
#define DEBUG_PRINT(str) // just leaves an empty definition without serial printing
#endif
```

## Creating objects and variables

After that we just setup all the objects and variables we'll use later:

```
// Accelstepper object
AccelStepper stepper(AccelStepper::DRIVER, 2, 3); // format: interface, step pin, direction pin (for shield: step:D2 and dir:D3)
// Instantiate a Bounce object for the start button
Bounce debouncer = Bounce(); 

// define input/button pin numbers
const int startButtonPin = 10;
const int leftEndStopPin = 9;
const int rightEndStopPin = 8;
const int startFromLeftPin = 11;
const int isTimelapseSpeedPin = 12;

// define output pin numbers
const int motorOffPin = 13;
const int ledPin = 5;

// set up LED and debug timers
Neotimer warningBlinkTimer = Neotimer(); 
Neotimer readyBlinkTimer = Neotimer(); 
Neotimer statusUpdateTimer = Neotimer(); 

// define analogue input for speed knob
const int speedPotPin = A0;
int speedInput = 0; // a variable to stare it in
int traverseSpeed = 0; // variable to hold speed when calculated

// variables to determine kind of traverse
bool startFromLeft = true;
bool isTimelapseSpeed = false;
```

## Setup state machine

As part of this, there is a section for the state machine itself:

```
// WARNING: values, order of items and total number of items must match the array below
enum possibleStates {
  INIT,
  TRAVERSING,
  ABORTED
};

// create an array of labels from the enum for debugging
// WARNING: this array must be updated if you change the enum
String stateLabels[3] = {
  "INIT",
  "TRAVERSING",
  "ABORTED"
};

// create a variable of this type
enum possibleStates currentState;

// keep track of whether the state has changed to limit status message updates
bool isNewState;
```
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

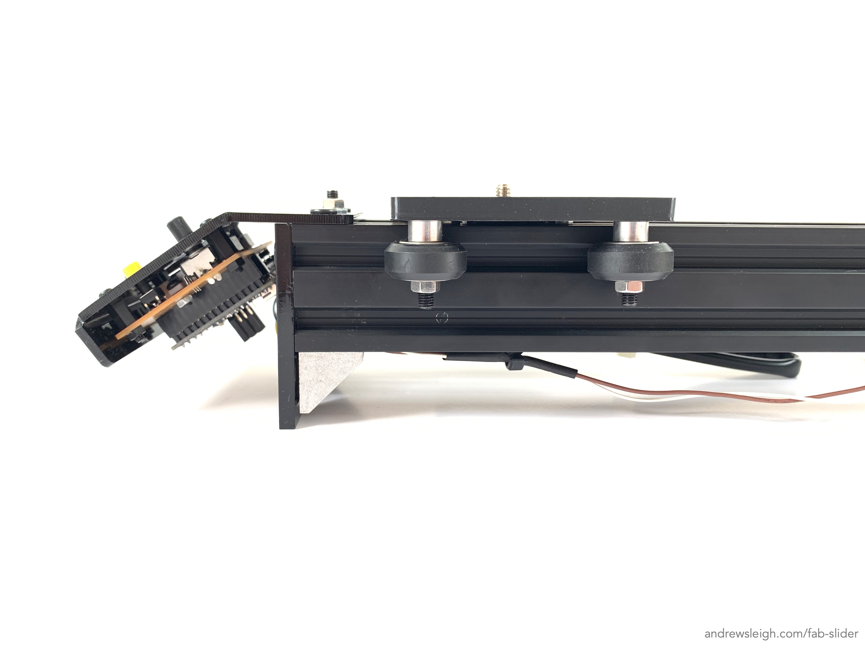
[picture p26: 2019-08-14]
images/2560px-wm/IMG_2669-2560px-wm.jpg

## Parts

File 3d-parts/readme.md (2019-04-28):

# Readme

These directories contain design files for all 3D parts of the assembly that aren't bought.

All parts are for version 1.

## Contents

* [v1/assembly/](v1/assembly/)
  * Entire assembly as a Fusion 360 archive file.
* [v1/gantry/](v1/gantry/)
  * STL file for 3D-printing a one-piece gantry (with separate D-ring cover plate)
  * DXF/EPS files for laser cutting a gantry out of sheet material to be glued together
* [v1/extrusion-end-caps/](v1/extrusion-end-caps/) –
  * STL file for 3D-printing extrusion caps and feet for the ends of the slider
  * DXF/EPS files for laser cutting caps and feet
* [v1/endstop-clip/](v1/endstop-clip/)
  * Clip that slots into the V-slot (3D/STL)
* [v1/idler-pulley-plate/](v1/idler-pulley-plate/)
  * Simple plate that holds the idler pulley at the far end of slider. (2D/DXF/EPS)
* [v1/motor-bracket/](v1/motor-bracket/)
  * Bracket that bolts through the end cap into the extrusion holes to hold a NEMA 17 stepper motor (3D/STL)

## 2D or 3D?

For some parts, both 2D files for the laser cutter, and 3D files for the 3D printer are provided. Choose whichever you prefer. The 2 end-caps are essentially flat pieces, so I would suggest cutting these from thick sheet material.

For more details see the [gantry assembly guide](v1/gantry/)

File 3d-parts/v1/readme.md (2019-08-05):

# Readme

These directories contain design files for all 3D parts of the assembly that aren't bought.

All parts are for version 1.

## Contents

* [assembly/](assembly/)
  * Entire assembly as a Fusion 360 archive file.
* [gantry/](gantry/)
  * STL file for 3D-printing a one-piece gantry (with separate D-ring cover plate).
  * DXF/EPS files for laser cutting a gantry out of sheet material to be glued together.
* [extrusion-end-caps/](extrusion-end-caps/) –
  * STL file for 3D-printing extrusion caps and feet for the ends of the slider
  * DXF/EPS files for laser cutting caps and feet.
* [endstop-clip/](endstop-clip/)
  * Clip that slots into the V-slot (3D: STL)
* [electronics-face-plate/](electronics-face-plate/)
  * Bent acrylic plate which the electronics are screwed onto.  (2D: DXF/EPS)
* [idler-pulley-plate/](idler-pulley-plate/)
  * Simple plate that holds the idler pulley at the far end of slider. (2D: DXF/EPS). This is ow deprecated, as the pulley mounting is built into the electronics faceplate.
* [motor-bracket/](motor-bracket/)
  * Bracket that bolts through the end cap into the extrusion holes to hold a NEMA 17 stepper motor (3D/STL).

## 2D or 3D?

For some parts, both 2D files for the laser cutter, and 3D files for the 3D printer are provided. Choose whichever you prefer. The 2 end-caps are essentially flat pieces, so I would suggest cutting these from thick sheet material.

The electronics faceplate is made form a single piece of flat acrylic, bent to shape along the score lines. 

For more details see the [gantry assembly guide](gantry/)

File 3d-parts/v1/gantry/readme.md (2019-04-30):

# Gantry Assembly guide

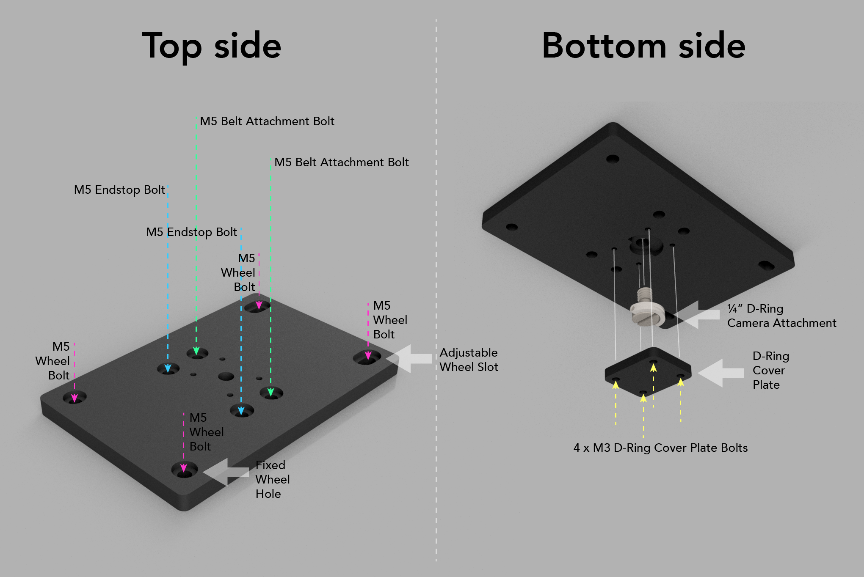
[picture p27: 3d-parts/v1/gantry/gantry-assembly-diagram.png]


The gantry has a number of parts:

* Main gantry plate
  * The large flat piece onto which everything else is attached, including the camera.
* D-Ring cover plate
  * A small extra plate that screws onto the underside of the gantry to capture the D-ring camera screw from underneath.
* Wheels
  * 4 wheel assemblies: 2 fixed, and 2 in slots so the tightness of the wheels against the rail can be adjusted.
* End-stop bolts
  * 2 long bolts (approx 40 mm) that pass through from the top of the gantry down to the underside. These make contact with the end-stops at each end of the slider. (These are slightly more offset from the centre than the belt attachment bolts.)
* Belt attachment bolts
  * 2 bolts, approx 20-30 mm, around which each end of the timing belt is wrapped, and then secured with a cable tie. (These are slightly offset from the centre of the gantry – the distance is determined by the radius of the belt pulleys.)

## 2D and 3D versions

The gantry is pretty much a flat piece, but has recesses for bolt heads, and in particular for the D-ring 1/4" screw onto which the camera is mounted. I 3D-printed this part, but it is possible to make it from 3 laser-cut sheets glued together.

### 3D-printed gantry

The bottom side (on the right) shows the printing support still to be removed where the D-ring camera screw sits.

The coverplate is a separate piece not shown here.

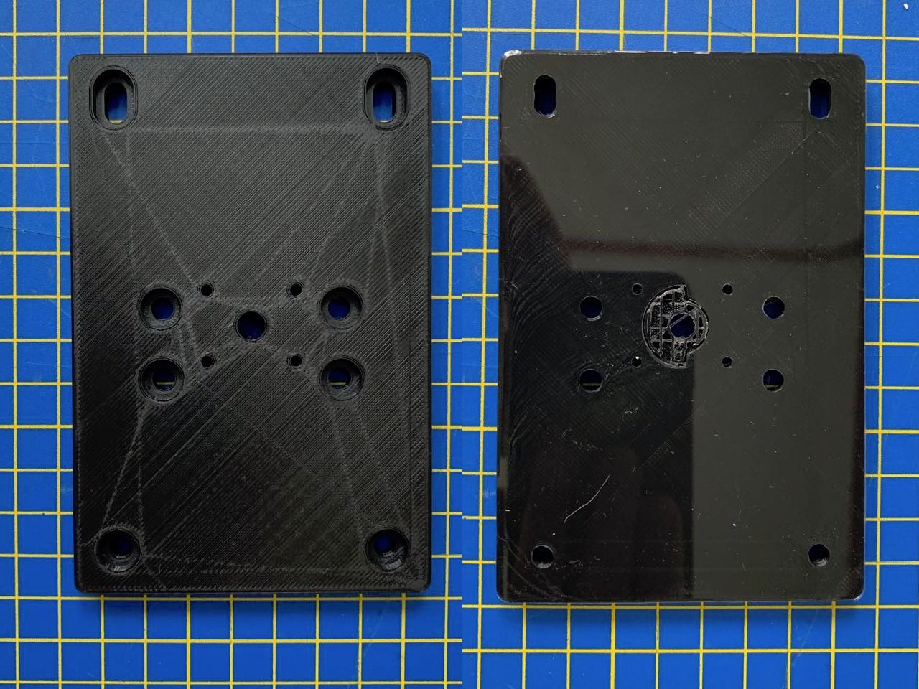
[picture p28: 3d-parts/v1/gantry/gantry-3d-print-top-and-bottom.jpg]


### Laser-cut gantry

The two main parts are simply glued together, with the cover plate screwed on after the D-ring screw has been placed in its cavity.

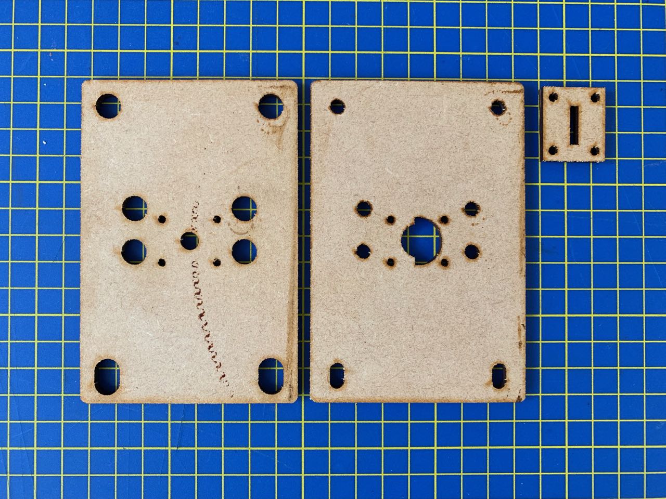
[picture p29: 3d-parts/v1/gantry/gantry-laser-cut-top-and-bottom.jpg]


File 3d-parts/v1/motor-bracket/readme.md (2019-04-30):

# Motor Mounting Bracket

This is a very simple bracket that mounts a standard NEMA 17-size motor through the end-cap piece into the central holes of  two pieces of 2040 extrusion mounted 40 mm apart.

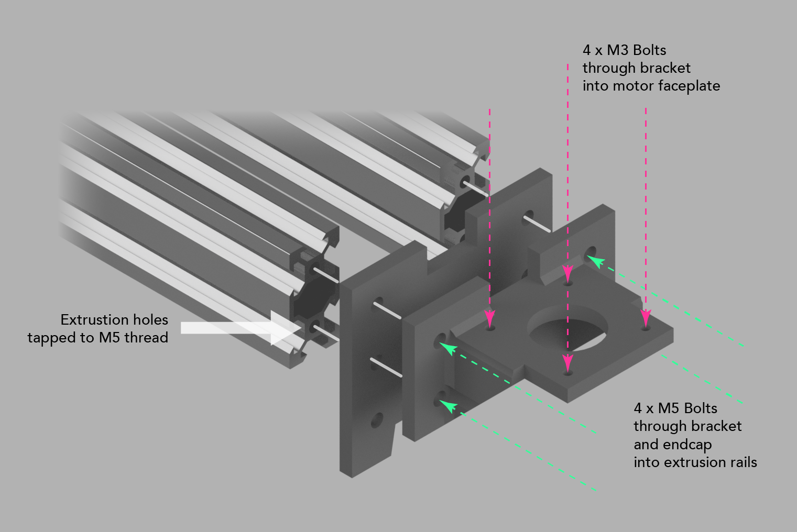
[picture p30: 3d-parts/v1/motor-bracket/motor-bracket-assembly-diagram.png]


(The part sandwiched between the bracket and the extrusion here is the [end cap](../extrusion-end-caps/).)

This mounting approach relies on the extrusion having M5 holes tapped into the central holes. Some suppliers (like Ooznest) will do this for you, or you can do it yourself.

If you don't have threads tapped in your extrusion, this style of attachment may not be the best approach.

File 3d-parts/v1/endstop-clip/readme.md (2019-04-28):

# Readme

Please note this rather cunning clip is not my design. It is taken, unmodified, from [Third Wheel Endstop Mount, V-slot](https://www.thingiverse.com/thing:2204123) by [thehans](https://www.thingiverse.com/thehans) licensed under the Creative Commons - Attribution - Share Alike license.

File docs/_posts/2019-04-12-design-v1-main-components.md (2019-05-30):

---
permalink: design-v1-main-components/
title: Main components
date: 2019-04-12
author: Andrew
layout: page
sort_id: 30
sort_tag: v1_design
---

## Sketch

This (bad) sketch shows one end of the slider from the top. The two lengths of 2020 extend to the left, the motor is mounted on the right with a right angle bracket which is fixed to the front plate of the motor, and to the central holes in each of the aluminium rails.

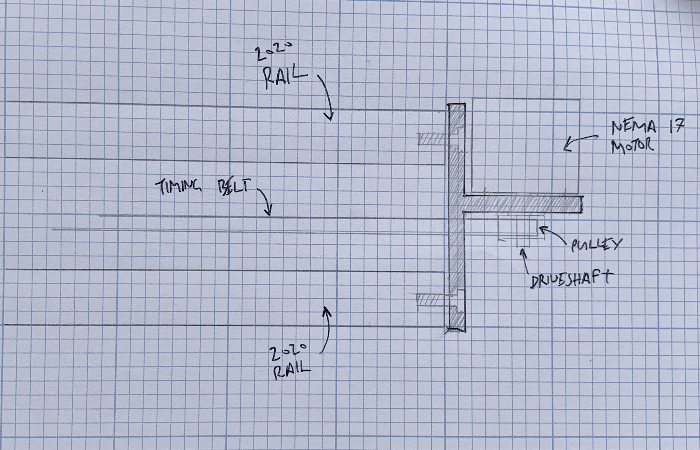
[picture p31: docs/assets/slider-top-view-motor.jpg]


## Main Components

The project can be split into a number of components. I'll address each on their own page:

* [Aluminium extrusion rails](../design-v1-rails/)
* [Stepper motor](../esign-v1-motor/)
* [Motor driver board](../design-v1-driver/)
* [Microcontroller board](../design-v1-microcontroller/)
* [Power supply](../design-v1-power/)
* [Gantry for camera](../design-v1-gantry/)
* [Endstops](../design-v1-endstops/)
* [User controls, brackets, feet, fixings and everything else](../design-v1-everything-else/)

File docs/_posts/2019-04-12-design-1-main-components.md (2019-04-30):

---
permalink: design-1-main-components/
title: Design 1 – Main Components
date: 2019-04-12
author: Andrew
layout: page
sort_id: 30
---

## Sketch

This sketch shows one end of the slider from the top. The two lengths of 2020 extend to the left, the motor is mounted on the right with a right angle bracket which is fixed to the front plate of the motor, and to the central holes in each of the aluminium rails.



## Main Components

### Rails

I want to use standardised aluminium extrusion for the rails. These provide the main structure of the slider, and are also the guide surface along which the gantry slides. This is a good guide: [Beginner’s Guide to Building Things With V-Slot Aluminum Extrusion](https://www.makeuseof.com/tag/beginners-guide-building-things-v-slot-aluminum-extrusion/)

#### Choosing a profile
There are different kinds of profile. I can't find a comprehensive list anywhere, but there do seem to be some common types, and others may only differ from these in non-essential ways.

The two main profiles seems to be B-Type and I-Type (__Bosch Rexroth__ and __Item__ respectively). The B-type profile has a stepped slot, whereas the I-type has a smooth curve.

RS Components sell [RS-Pro branded extrusion](https://uk.rs-online.com/web/p/tubing-struts/8508476/). This has a 5 mm groove, and a 4.3 mm central hole. According to [this chart](https://www.boltdepot.com/fastener-information/metric-tap-drill-size.aspx) that can be tapped for a 5 mm thread.

They also have Bosch Rexroth branded extrusion with a 6 mm groove and a 5.5 mm central hole. Using that same table, that's a little off for tapping to a 6 mm thread, so I wonder if this is an imperial sizing?

There is also a newcomer to the field: V-type. From the [Beginner’s Guide to Building Things With V-Slot Aluminum Extrusion](https://www.makeuseof.com/tag/beginners-guide-building-things-v-slot-aluminum-extrusion/):

> T-Slot has a T-shaped groove on each side.
> V-Slot is similar, but it has a slight bevelled edge.
While this may seem like only a minor difference, it has a big impact in their use. V-Slot allows bearings and wheels to sit inside the profile, meaning it can also double as linear rail, greatly reducing the cost of parts for motion control.

> The two are somewhat interchangeable, but it’s usually best to stick with one type per project. Basic parts like brackets and T-Nuts work fine on either, however slightly more specialist parts — such as bearings or unusual joints — may only work on one or the other. Also, if you are mixing and matching parts, you may need to change or adapt your design, and have to purchase more lengths of one or the other extrusion.

> V-Slot was created by Mark Carew of OpenBuilds and is open source.

The V-type, as the name suggests, has a straight V-shaped bevel. I would say B-type or V-type would be best to take bearings depending on cost and availability (the latter is less of an issue if they can be easily swapped out for another type). V-slot accepts M5 bolts, so I think – at this stage – that V- and I-type profiles should be quite interchangeable.

#### Choosing size

I suspect two 2020 profile rails will be enough for this small span. 2040 mounted vertically would give me more rigidity. And the [8040 C Beam](https://ooznest.co.uk/product/c-beam-linear-rail-cut-to-size/) would be even more rigid:



Ooznest has a [guide to help you estimate deflection](https://ooznest.co.uk/wp-content/uploads/2018/05/How-To-Estimate-Deflection.pdf).

In my case, the calculation looks like this:



Let's plug in some numbers:

* Mass of the load: 1kg (roughly, for an SLR camera)
* F = Mass x Gravity = 1 * 9.81 = 9.81N
* L = 0.5m
* I (moment of inertia) = 6.988 * 10<sup>-9</sup> (for 2020 profile)
* E (modulus of elasticity) = 68.9 GPa (gigapascals) =  68.9 * 10<sup>9</sup> Pa

Therefore deflection  
= (9.81 * (0.5)<sup>3</sup>) / (48 * 68.9 * 10<sup>9</sup> * 6.988 * 10<sup>-9</sup>)  
= 1.22625 / 23110.7136  
= 0.000053 m  
= 0.053 mm  

So nothing to worry about at this length. However, if I made a 1 m long slider, deflection under ideal conditions for a 1 kg load would come out at: 9.81 / 23110.7136 = .00042 m = .42 mm. So for that span it might be worth using a more rigid profile.

For now, I'll go with 2020. However, there is one other advantage to a larger profile such as 2040. That has two holes at each end, allowing for more robust assembly. I'm concerned that the 2020, with only one hole at each end might twist in the assembly, causing the gantry to move poorly.

#### Choosing length

While a bigger slider is always more useful, a smaller one is cheaper, and easier to store, so I think a better target for a first build. If I decide to remake it, I can always disassemble the first version and re-use some parts for a bigger one.

**So – all other things being equal – I'll go for a 50 cm length.**

#### Prices

[2 x 50 cm 2020 V-Slot from Ooznest](https://ooznest.co.uk/product-category/parts/mechanical-parts/v-slot-extrusions/): £9.60 + postage

[2 x 50 cm 2020 IR Range Aluminium Profile (I-type) from KJN](): £7 + postage

[50 cm 8040 C-Beam from Ooznest](https://ooznest.co.uk/product/c-beam-linear-rail-cut-to-size/): £14.80 + postage (both ends tapped with 5mm holes: £16.24. I should be able to tap these myself if needed). I like this, but it's not a standard profile,

[1 m I-type from RS Components](https://uk.rs-online.com/web/p/tubing-struts/8508476/): £6.90 + postage

WIP: 2 x 40 cm 2040

### Motor

This project requires a stepper motor. For background on motors, see:
* [Motors – code, circuits, & construction](http://www.tigoe.com/pcomp/code/circuits/motors/)

On steppers specifically:
* [Stepper Motor Quickstart Guide - SparkFun Electronics](https://www.sparkfun.com/tutorials/400)
* [What is a Stepper Motor? -  Adafruit Learning System](https://learn.adafruit.com/all-about-stepper-motors)

Figuring out which size of motor is complicated, so instead, I went for the soft option, and asked some people who have worked with them, and looked at what other projects use. The consensus was to go for the NEMA 17. You might think NEMA is a brand name for a motor, but no, NEMA stands for [National Electrical Manufacturers Association](http://en.wikipedia.org/wiki/National_Electrical_Manufacturers_Association). The 17 refers to the size of the faceplate - 1.7" x 1.7".

According to <https://reprap.org/wiki/NEMA_Motor>
> Some (all?) NEMA 17 motors (is this specified in the standard?) have blind mounting holes 4.5 mm deep, tapped to accept M3x.50 metric bolts. The 4 mounting holes are in a square 31.0 mm (1.220 inch, about 7/32) center-to-center. The holes in the part that needs to be bolted to the NEMA 17 motor typically need to be reamed out with a 1/8" drill bit to allow the M3 bolt to pass through. The drive shaft is typically 5 mm dia.

According to <https://learn.adafruit.com/all-about-stepper-motors/types-of-steppers>:
>The NEMA numbers define standard faceplate dimensions for mounting the motor. They do not define the other characteristics of a motor. Two different NEMA 17 motors may have entirely different electrical or mechanical specifications and are not necessarily interchangeable.

Specs typically seem to vary on a number of common parameters:
*  Number of steps per full rotation: 200 (1.8&deg; steps) or 400 (0.9&deg; steps). For timelapse, I would assume a finer step gradation would be better.
* Current draw (i.e. power). These vary from about 0.3A to 2A. Some motor current are listed as 'per phase' so I don't know how comparable these are.
* Unipolar or bipolar – from [the Adafruit guide](https://learn.adafruit.com/all-about-stepper-motors/types-of-steppers):
  * Unipolar drivers, always energize the phases in the same way. One lead, the "common" lead, will always be negative. The other lead will always be positive. Unipolar drivers can be implemented with simple transistor circuitry. The disadvantage is that there is less available torque because only half of the coils can be energized at a time.")
  * Bipolar drivers use H-bridge circuitry to actually reverse the current flow through the phases. By energizing the phases with alternating the polarity, all the coils can be put to work turning the motor.
* 2-phase or 4-phase – from [the Adafruit guide](https://learn.adafruit.com/all-about-stepper-motors/types-of-steppers):
  * A two phase bipolar motor has 2 groups of coils. A 4 phase unipolar motor has 4. A 2-phase bipolar motor will have 4 wires - 2 for each phase. Some motors come with flexible wiring that allows you to run the motor as either bipolar or unipolar.

<!-- One question for me is: what is the speed range of each motor? I'm looking for wide range of traverse speeds, from say 50 cm in 50 minutes, to 50 cm in 5 seconds. Let's see what kinds of RP ranges that would cover

Don't think this is an issue, as for slow speeds, I can just move one step at a time, with delays between -->

Lets look at some actual motors for sale:

[**Ooznest**](https://ooznest.co.uk/product/nema17-stepper-motors/)
* Bipolar
* 2-phase
* 1.33A – 2A per phase (but note this motor is rated at 2.8V, not 12V like most others)
* 200 or 400 steps per rotation

Their cheapest motor is a 200 step 1.4A model for £9.90 (NEMA17 Stepper Motors - 1.8° - 1701HS140A - 21oz - 1.40A)

[**Cool Components**](https://coolcomponents.co.uk/products/stepper-motor-with-cable)

This is a Sparkfun model, for about £15:

* Step Angle (degrees) :1.8
* 2 Phase
* Rated Voltage : 12V
* Rated Current : 0.33A
* Holding Torque : 2.3kg*cm

[**Adafruit**](https://www.adafruit.com/product/324) seem to have something quite similar. ($14, 350 mA, 4-wire bipolar, 1.8° steps (200/revolution))

[Digikey also has some pretty similar models](https://www.digikey.co.uk/products/en/motors-solenoids-driver-boards-modules/stepper-motors/179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)

Adafruit specify the stepper above for their slider project, so this seems like a pretty good place to start.

### Motor driver

There are lots of different boards, based on different chips. So how do you choose?

From [How to Make a Robot - Lesson 5: Cho - RobotShop Community](https://www.robotshop.com/community/tutorials/show/how-to-make-a-robot-lesson-5-choosing-a-motor-controller)

> 1 Is the motor you selected unipolar or bipolar? Choose a stepper motor controller type accordingly, though a growing number are able to control both types. The number of leads is usually a dead give-away of the motor type: if the motor has 4 leads, then it is bipolar; should it have 6 or more leads, then it is unipolar.
> 2 Choose the motor controller voltage range to match your motor’s  nominal voltage .
> 3 Find out how much current per coil your motor requires, and find out how much current (per coil) the stepper motor controller can provide.If you cannot find the current per coil, most manufacturers list the coil impedance, R . Using Ohms Law (V=IR), you can then calculate the current (I).
> 4 As with DC motor controllers, the control method is an important consideration.

From [Stepper Motor Control - Adafruit Motor Selection Guide](https://learn.adafruit.com/adafruit-motor-selection-guide/stepper-motor-control):

> Stepper motor controllers are more complex than DC motor controllers. Driving a bipolar motor with microstepping requires 2 complete H-bridges and 2 channels of PWM.
>
> The versatile Adafruit Motor Shield V2 has 4 H-bridges and can drive as many as 2 steppers. What’s more, it is stackable to control dozens of motors.

From [Driving a Stepper - All About Stepper Motors - Adafruit](https://learn.adafruit.com/all-about-stepper-motors/driving-a-stepper#simple-dual-h-bridge-driver-3-8):

> Simple Dual H-Bridge Driver
> Driving a bipolar motor requires 2 full H-bridges so it can reverse the current to the phases. H-bridges can be tricky to build from scratch. But there are plenty of H-bridge chips available to simplify the task.>
> The L293D is one of the most popular and economical chips. These can be found at the heart of most first-generation motor shields, including the incredibly popular V1 Adafruit Motor Shield.

The motors I'm looking at are bipolar, with 4 leads, and run at 12 V and 0.33/0.35 A.

It looks like an [Allegro 3967](https://cdn.sparkfun.com/datasheets/Robotics/A3967-Datasheet.pdf)-based driver board should work. This chip is rated to ±750 mA, 30 V

* This is the basis of the Sparkfun [Easy Driver](https://www.sparkfun.com/products/12779) ($15)
* SeeedStudio also have a similar board: [Stepper Motor Driver V4.5](https://www.robotshop.com/en/seeedstudio-stepper-motor-driver-v45.html) ($13)

This board design is open source ([documented here](https://www.schmalzhaus.com/EasyDriver/)), so I could, for version 2, fab my own using this chip. Perhaps with an integrated microcontroller. It also means there are numerous cheaper knock-offs available:

* [EasyDriver Stepper Motor Controller A3967](https://www.robotshop.com/uk/easydriver-stepper-motor-controller-a3967.html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) (£5.70)
* [This on Amazon](https://www.amazon.co.uk/Aihasd-EasyDriver-Stepper-Development-Arduino/dp/B00WR8IQHW) (£2.80)
* [This on eBay](https://www.ebay.co.uk/p/EasyDriver-Shield-Stepping-Stepper-Motor-Driver-V44-A3967-for-Arduino/2169027753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) (£1.30)

There is another Allegro chip, the [A4988](https://cdn.sparkfun.com/datasheets/Robotics/A4988-Datasheet.pdf), which is rated to 35 V and ±2 A.

* This is used in Sparkfun's [Big Easy Driver](https://www.sparkfun.com/products/12859) ($20)
* Pololu also have a much cheaper board: [A4988 Stepper Motor Driver Carrier](https://www.pololu.com/product/1182) $6

Adafruit have a nice board, the [Motor/Stepper/Servo Shield for Arduino v2 Kit - v2.3](https://www.adafruit.com/product/1438), based on the TB6612, which can drive up to two steppers at 1.2 A per channel. This is $20, so comparable to other brand-name boards that can only drive one stepper.

There are many others, including the [STMicroelectronics L293D](http://www.st.com/st-web-ui/static/active/en/resource/technical/document/datasheet/CD00000059.pdf) used in the [Adafruit Arduino Motor Shield](http://www.adafruit.com/index.php?main_page=product_info&products_id=81) and [Toshiba TB6600](http://www.semicon.toshiba.com.cn/info/docget.jsp?type=Catalog1&lang=en&pid=TB6600HG) used in the [PiBot TB6600 Stepper Driver](http://reprap.org/wiki/PiBot_TB6600_Stepper_Driver) and also in the _fab-able_ [satstep6600](https://github.com/satstep/satstep6600).

[Reprap also has a good list of different driver chips.](https://reprap.org/wiki/Stepper_motor_driver)

I think a 3967-based driver is enough for me to start with, and keeps costs down.

### Microcontroller

Although I'm interested in making an integrated board that incorporates an AVR microcontroller and one or more stepper drivers, it's also a valid choice to design around a microcontroller that people already have.

For the Easy Driver-style boards, hookup varies depending on whether you want to control the microstep resolution with the Arduino (which requires 3 more pins).

The [simplest hookup](http://www.schmalzhaus.com/EasyDriver/Examples/EasyDriverExamples.html) just uses 2 pins to control step and direction, with power coming from a separate supply:



There is also an example given for multiple steppers, for which you need to use a library:

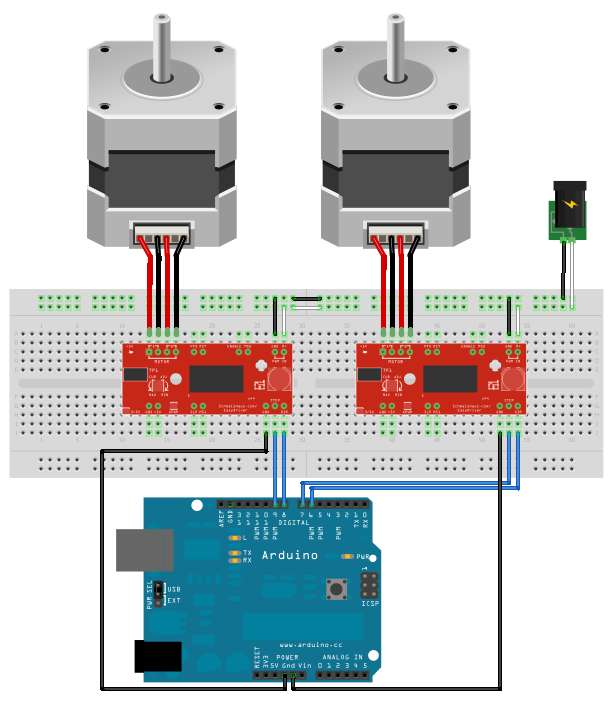
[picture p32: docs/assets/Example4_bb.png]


Again, this just uses 2 pins per motor. If I want to use two steppers, and also use all the control pins on the drivers, this may cause problems down the line...

The [Adafruit board](https://www.adafruit.com/product/1438) uses I2C, making it very easy to control multiple motors:
> Instead of using a latch and the Arduino's PWM pins, we have a fully-dedicated PWM driver chip onboard. This chip handles all the motor and speed controls over I2C. Only two data pins (SDA & SCL in addition to the power pins GND & 5V) are required to drive the multiple motors, and since it's I2C you can also connect any other I2C devices or shields to the same pins. This also makes it drop-in compatible with any Arduino, such as the Uno, Due, Leonardo and Mega R3.

Either way, for now, I should be able to get away with a standard Arduino Uno, and may be able to specify a smaller board like the Pro Mini, or maybe, for version 2, an ATtiny-based DIY board if I need only a few pins.

### Power supply

From [Stepper Motor Quickstart Guide - SparkFun Electronics](https://www.sparkfun.com/tutorials/400):
>  Stepper motors require more power than can be supplied by the Arduino. In this example we will be powering the Uno with a 12V external supply. Notice that the power input (M+) on the EasyDriver is attached to the Vin pin on the Arduino. This will allow you to power both the Arduino and the motor with the same power supply.

From https://learn.adafruit.com/motorized-camera-slider-mk3?view=all#12v-power-14-1
> 12V Power
> To properly power the stepper motor, you need at least 12V. A USB battery pack typically is only 5V and will not provide enough juice to push the weight of a camera (be it a lightweight GoPro or Mobile Phone). I highly suggest using either a 12V power wall adapter or 12V battery pack.
> Wall Adapter
> I mostly use the camera slider indoors. Having it plugged into the wall is nice because I don't have to worry about batteries getting low and dying. This  [12V DC 1000mA power adapter](https://www.adafruit.com/product/798)  works great with this project.

The Arduino Uno has a barrel jack power input, and can pass through 12V power to the driver board, so I think this is the best way to go. I have several old 12V wall-warts that can supply 1 or 2 A of current.

For portable power, an [8 x AA battery power pack](https://www.adafruit.com/product/875) is probably the best option.

### Gantry

The gantry is basically just a flat plate with mounting holes for attaching different devices, and for the wheels and timing belt.

Ooznest sell an [aluminium gantry plate](https://ooznest.co.uk/product/c-beam-gantry-plate-kit/)for the 8040 V-slot C-beam (in a kit form with delrin wheels for £25). This C-beam has a 40 mm channel down the middle, so it should be adaptable for two lengths of 2020 mounted 40 mm apart.



They also have a [simpler plate](https://ooznest.co.uk/product/v-slot-gantry-plate-small-kit/) designed to straddle a single 2020 rail. (£24 in a kit with 4 wheels).



These are really nice plates, and you could certainly make something similar out of laser-cut acrylic.

#### Mounting a camera

Camera mounts are standardised around a 1/4" screw. Even mounts for phones typically have a 1/4" threaded hole so thy can be mounted on standard camera accessories, like tripods. So this is a good fitting onto which I could fit any number of off-the-shelf mounting parts, such as this [camera mount](https://www.adafruit.com/product/2464).

An aluminium baseplate could have a threaded hole to accept a 1/4" bolt. I can't create a threaded hole in an acrylic baseplate but I could create a two-layer plate, where the top layer has a hexagonal hole to capture a nut into which a bolt could be threaded.

Note: the camera needs to be able to site flush against the top face of the gantry. So any other fixings – for example the timing belt, or the bolts for the wheels – need to be recessed or otherwise out of the way. With a metal (or wooden) plate, this is easy enough, you could use countersink-headed bolts. But you can't laser-cut acrylic with countersink holes, so again, I'm leaning towards a 2-layer design. 3D printing would be another option.

#### Attaching the timing belt

The Adafruit slider uses a vertical drive shaft, meaning that the timing belt is also vertical. They use a nice kinked channel in the gantry plate to hold the (continuous loop of belt) belt in place.



This picture also shows the use of a belt tightener.

The Ooznest design uses a drive shaft in a horizontal orientation, so the belt is transposed through 90&deg;. You can see the slots on the edges of the gantry plate through which you could thread each end of the timing belt, to be secured with a cable grip.



This approach allows you to cut the belt to whatever size works. I think this is a better approach for me, assuming I use a laser-cut gantry.

#### Mounting bearings

This image of the Ooznest gantry show the kind of method I'd like to use. As they use an aluminium plate, they're able to cut recessed holes for the bolt heads to allow them to sit flush with the top surface. I think I could achieve the same effect with a 2-layer laser-cut acrylic plate. Or by conventional manual countersinking in a MDF laser-cut plate.



Some kits (e..g the Ooznest kit) use eccentric spacers to allow the wheels to be adjusted in fine increments. A simpler – and perhaps adequate – solution would be to use slots rather than round holes to accept the wheel bolts.

### Wheels/bearings

I'm looking to mount 4 wheels on bearings in a horizontal orientation underneath my gantry.
It's possible I can[ 3D-print the wheels](https://www.thingiverse.com/thing:1452180) themselves, but I'd still need the bearing, bolt and spacer assembly.
So I'm inclined, for version one, to buy the complete assembly, and see if I can swap out some commercial parts for DIY versions later. Apart from anything, I'd like to see what difference it makes to the motion of the gantry. But wheel kits are expensive:

* [Ooznest Delrin Dual V Wheel](https://ooznest.co.uk/product/delrin-dual-v-wheel/), including M5 bolt and 6mm spacer: £4.44 each
* [Ooznest Mini V Wheel Wheel](https://ooznest.co.uk/product/mini-v-wheel/), including M5 bolt and 6mm spacer: £3.44 each

Alternatively, cheaper versions are available on Amazon, etc. For example, [BIQU Equipment Wheel with Bearings (Pack of 5)](https://www.amazon.co.uk/BIQU-Printer-Plastic-Bearings-Passive/dp/B06X9Q9Y8V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) (£6)
 or [Samje Wheels (Pack of 5)](https://www.amazon.co.uk/Samje-Printer-Plastic-Bearings-Passive/dp/B07F61MXGR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) (£9)

### Belt

GT2 Belt seems to be pretty standard. That means it has a pitch of 2 mm between the teeth. The 6 mm wide belt seems to be the most common.

* [Ooznest](https://ooznest.co.uk/product/gt2-open-timing-belt-per-metre/): £2.90/metre
* [Adafruit](https://www.adafruit.com/product/1184): $10 / 1164mm long (continuous loop)

### Pulleys and/or bearings

I'll need at least one pulley (a toothed wheel), that can be mounted to the motor drive shaft. At the other end of the rail, I can use a bearing to allow the belt to move freely.

The image below shows the belt mechanism at one end of the Adafruit slider. Note how a smooth bearing is used, not a toothed pulley:



Pulleys are specified by a given number of teeth, for a certain pitch of belt. e.g. a `30 tooth GT2 pulley`. I need a 5 mm bore for the motor drive shaft, with fixing via a grub screw, and a width of 6 mm or more for the 6 mm belt.

One factor I might want to  consider here is the diameter of the pulley. [According to Ooznest](https://ooznest.co.uk/product/gt2-pulleys/), a 30 tooth **GT3** pulley (note: the description here says GT3, not GT2, but I think that may be a typo) will allow the belt to loop around both sides of a 20 mm extrusion.

I plan to run the timing belt in the cavity between two rails of aluminium extrusion, so this may not be an issue. However, if I want to include an angled rod between the two rails to pivot the gantry along its traverse, I might want to use a bigger pulley to leave some space here. The pulley and the opposite-end bearing should have roughly the same diameter.

Fortunately, [it is possible to calculate the diameter of a pulley](https://www.pfeiferindustries.com/timing-belt-pulley-pitch-diameter-outside-diameter-charts) if you know the number of teeth and the pitch.

Diameter   
= Number of teeth * Pitch / Pi  
= 30 * 2 mm / 3.14  
= 19.1 mm

For a 20 tooth pulley, this works out at 12.7 mm. Obviously this gives you the diameter on the inside of the belt, so to check for clearances, you need to allow for the thickness of the belt, and also the diameter of any fences on the pulley.

It's [possible to laser-cut pulleys](http://fab.academany.org/2018/labs/fablabbrighton/students/andrew-sleigh/assignments/2018/05/09/wk15-machine-building.html), and I think this would be an experiment worth doing, to compare with commercially made pulleys.

Pulleys:

* [Adafruit Aluminum GT2 Timing Pulley - 6mm Belt - 36 Tooth - 5mm Bore](https://www.adafruit.com/product/1253): $12
* [Ooznest GT2 Pulley 20 Tooth](https://ooznest.co.uk/product/gt2-pulleys/): £2.90
* [Ooznest GT2 (**I think**) Pulley 30 Tooth](https://ooznest.co.uk/product/gt2-pulleys/): £8.75

Bearings:

* Ooznest only sell 5 mm wide bearings. If I'm using a 6 mm belt, these won't be big enough
* [Amazon 10 x 26 x 8 mm bearings, pack of 3](https://www.amazon.co.uk/Metallic-Sealed-Groove-Bearing-6000Z/dp/B07MX91G6Q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) (£3.50)
* [RS have many 6-7 mm wide bearings at 19 mm diameter](https://uk.rs-online.com/web/c/pneumatics-hydraulics-power-transmission/power-transmission-rotary-bearings/ball-bearings/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,4294536636,4294845442&sort-by=P_breakPrice1&sort-order=asc&pn=1) (around £2 each)

You can also get 'idler pulleys', essentially a pulley mounted on a bearing, which might be a better choice for the end opposite the motor.

* Amazon: [20 teeth 5mm Bore 6mm width (Pack of 5)](https://www.amazon.co.uk/BIQU-20Teeth-Aluminum-Timing-Printer/dp/B06VSL9W9L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) (£7)

Or you can buy complete kits of belts, pulleys and idler pulleys ([This, £15 on Amazon](https://www.amazon.co.uk/KeeYees-Timing-Tensioner-Torsion-Printer/dp/B07JGXG7S2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), or [this, just the belt and 2 pulleys for £9](https://www.amazon.co.uk/JSDL-Timing-Pulley-2GT-6mm-Opening/dp/B06XQ333PN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))

### End caps / feet

WIP

### Controls and screen

WIP!

### End stops

I have some end-stop switches left over from a previous project.

### Tripod mount

This is a 'nice-to-have' feature, but shouldn't be difficult to implement. I just need a plate on the bottom of the rails with a threaded hole (or captured nut) to accept a 1/4" (or possibly 3/8") UNC threaded bolt. These are the [standard sizes for tripod mounts](http://www.photokonnexion.com/photography-thread-size/):

| Diameter (inch) | Diameter (mm) | Thread size |
| :---: | :---: | :---: |
| 1/4 | 6.3500 | 20 |
| 3/8 | 7.9375 | 16 |

### Assembly brackets and casings

#### Motor

There are many [3D designs on Thingiverse](https://www.thingiverse.com/search?q=nema+17+bracket&dwh=1005cb30d3341f54).

The sketch at the top of the page shows the bare minimum I'd need to do to mount the motor to the rails in the right orientation. This needs more work, perhaps in Fusion 360.

#### Belt bearing

Unless I use an idler pulley (which has fences on either side of the rail), this might need some sort of guides to stop the belt sliding off the bearing.

Ideally, (as on the Adafruit slider bearing bracket) the bolts in this bracket should fit into slots, so the bracket itself can be moved back and forth to adjust belt tension (just like the rear wheel on a single speed bike).

#### Microcontroller and driver boards

I think for version 1, this could be an entirely separate assembly, since only an electrical connection is needed between the boards and the motor.

### Fixings

It would be nice if the design could standardise on one bolt size, say M5, with one head type. For example, if all bolts had Allen key heads of the same size, you could attach the correct key somewhere on the frame of the machine, for easy adjustment or tightening.

(Maybe I should get an assortment set?)

#### T Nuts and brackets?

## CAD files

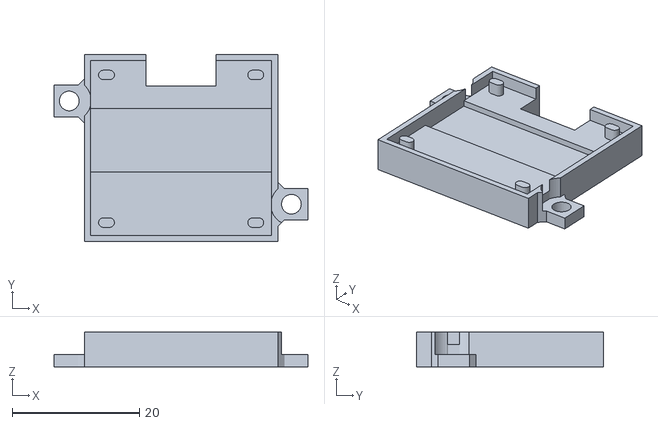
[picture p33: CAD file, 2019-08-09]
3d-parts/v1/electronics-face-plate/oled-mount.stl
40.0 x 29.5 x 5.50

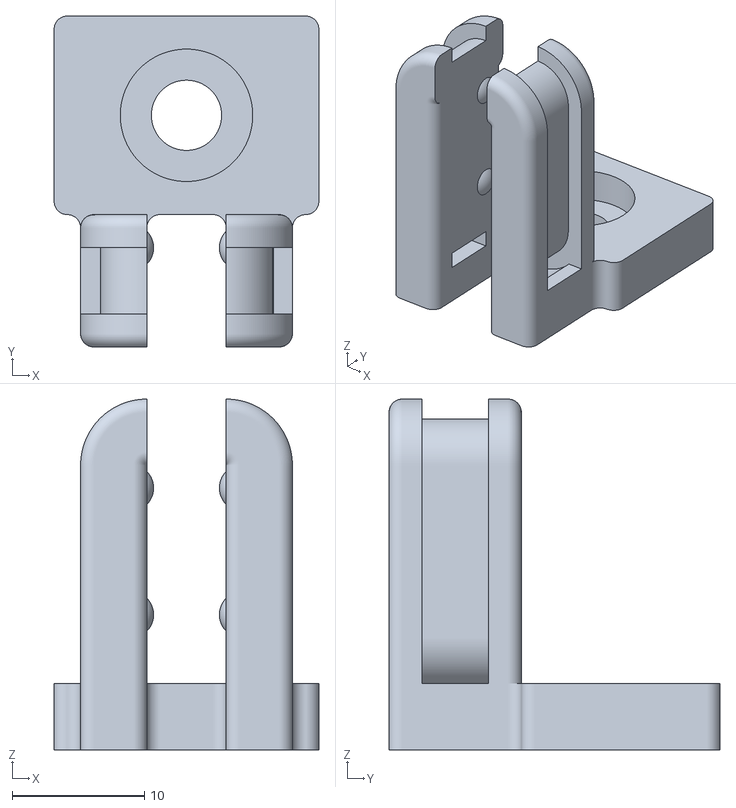
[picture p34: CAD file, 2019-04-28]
3d-parts/v1/endstop-clip/endstop_mount_mirrored.stl
20.0 x 25.0 x 26.5

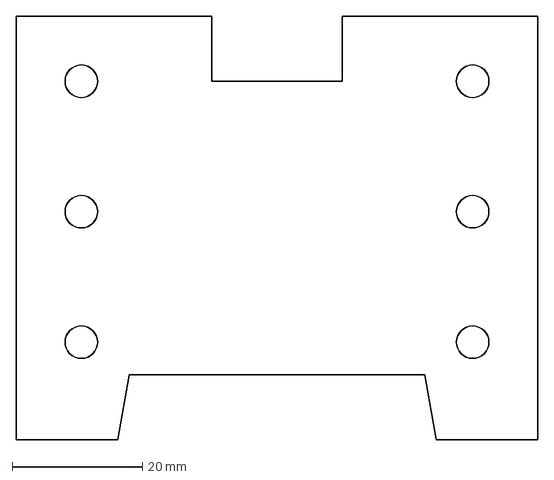
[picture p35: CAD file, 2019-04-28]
3d-parts/v1/extrusion-end-caps/end-cap-2D.dxf
80.0 x 65.0 mm

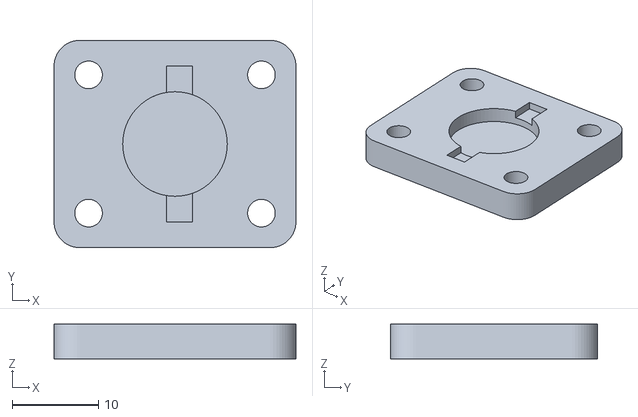
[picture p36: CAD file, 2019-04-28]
3d-parts/v1/gantry/gantry-d-ring-coverplate.stl
28.0 x 24.0 x 4.00

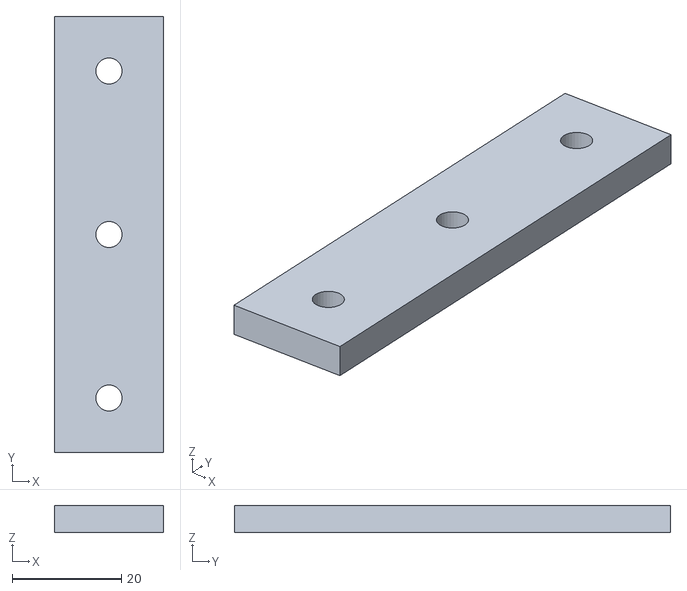
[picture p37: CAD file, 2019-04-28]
3d-parts/v1/idler-pulley-plate/idler-pulley-plate.stl
20.0 x 80.0 x 5.00

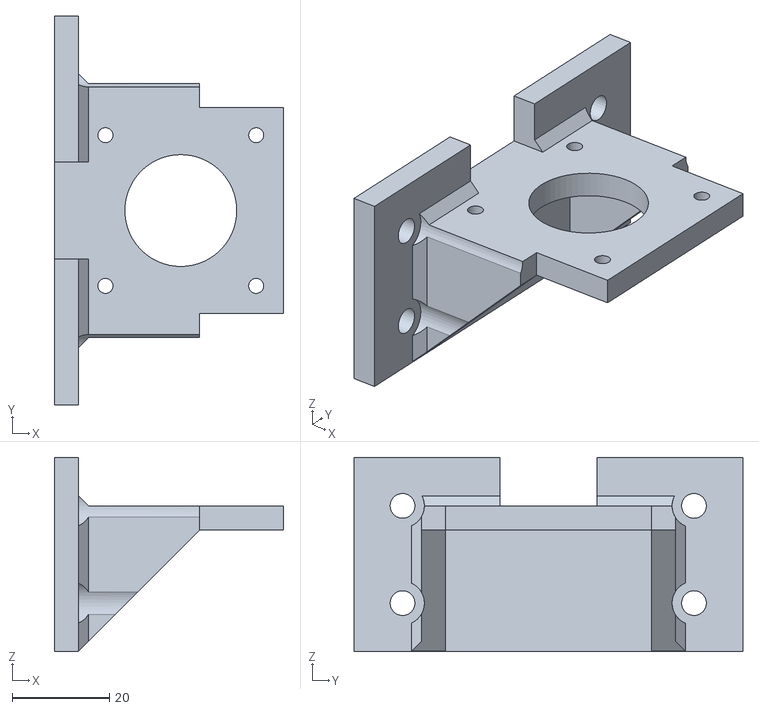
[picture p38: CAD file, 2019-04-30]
3d-parts/v1/motor-bracket/motor-bracket.stl
47.2 x 80.0 x 40.0

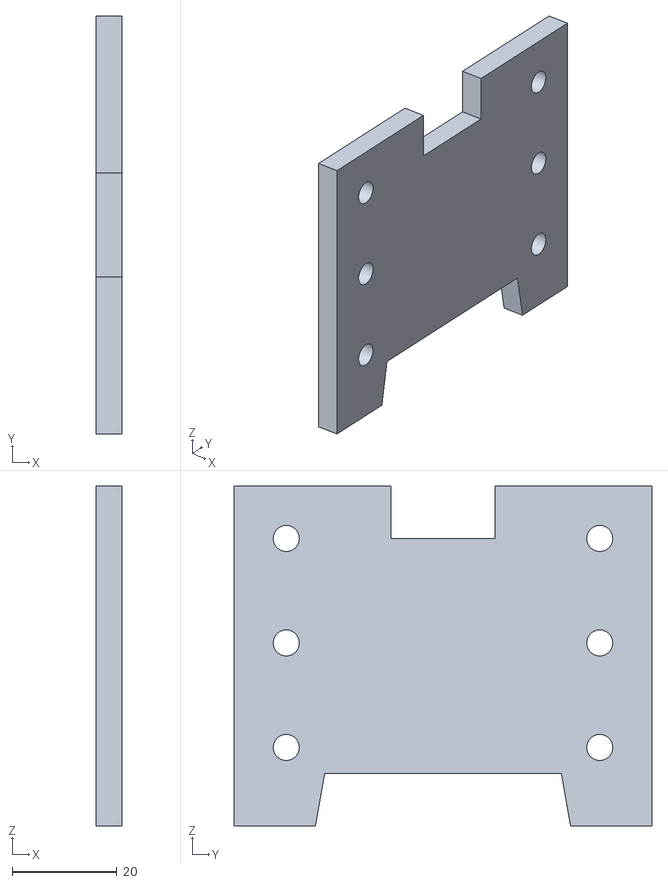
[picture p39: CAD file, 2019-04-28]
3d-parts/v1/extrusion-end-caps/end-cap-3D.stl
5.00 x 80.0 x 65.0

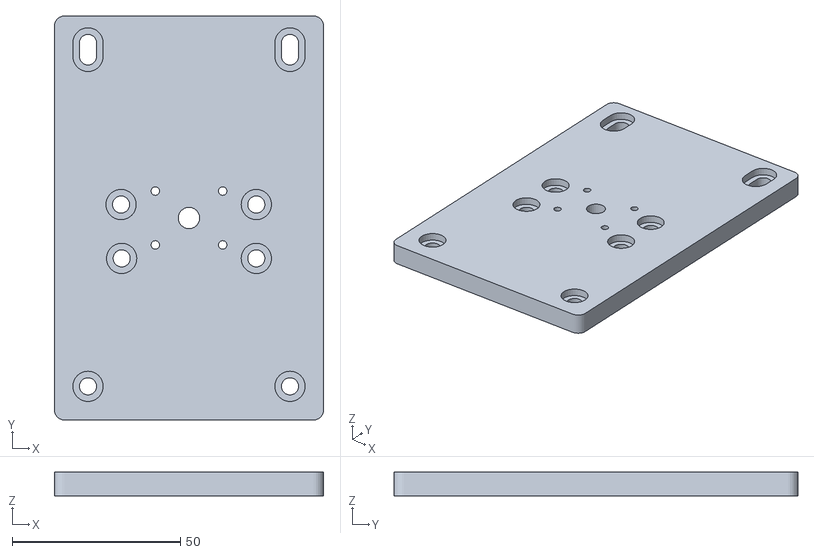
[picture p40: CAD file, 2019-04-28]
3d-parts/v1/gantry/gantry.stl
80.0 x 120.0 x 7.00

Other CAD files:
3d-parts/v1/electronics-face-plate/flat-electronics-faceplate.dxf
3d-parts/v1/assembly/fab-slider-v1.f3z
3d-parts/v1/idler-pulley-plate/idler-pulley-plate.dxf

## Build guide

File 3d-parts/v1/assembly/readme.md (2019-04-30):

# Whole Assembly as Fusion 360 File

[Shared Fusion 360 link](https://a360.co/2WaDq9M)  
[Download Fusion 360 archive file](fab-slider-v1.f3z)

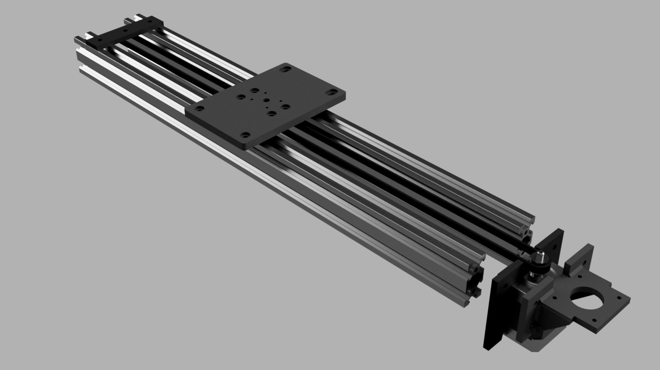
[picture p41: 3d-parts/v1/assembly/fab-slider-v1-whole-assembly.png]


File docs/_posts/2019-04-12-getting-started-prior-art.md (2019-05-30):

---
permalink: getting-started-prior-art/
title: Prior art
date: 2019-04-12
author: Andrew
layout: page
sort_id: 11
sort_tag: v1_getting_started
---

#### Commercial motorised sliders
There are many similar looking Chinese sliders on Amazon, at about £320-£360, for example:
[GVM Camera Slider Track](https://www.amazon.co.uk/GVM-Sliders-Motorized-Panoramic-Shooting/dp/B07BMLD4N4?ref_=fsclp_pl_dp_1):

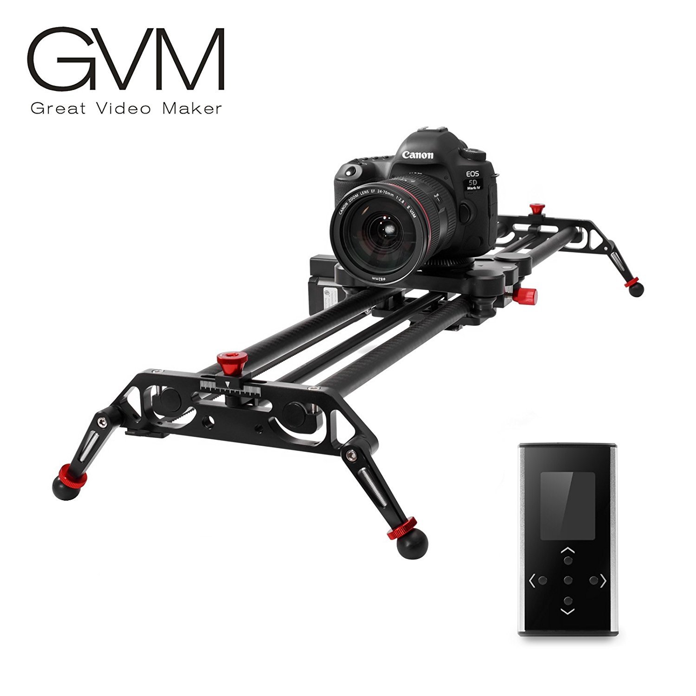
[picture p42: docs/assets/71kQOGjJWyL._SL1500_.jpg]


These mount the motor on the gantry and use carbon fibre poles as the slide rails.
They have a nice mechanism to allow rotation of the gantry across the traverse without using a second motor.
They mount the motor to the gantry and move it along a timing belt stretched along the rails.

Ooznest sell the [Ratrig V-Slider DIY Camera Slider kit](https://ooznest.co.uk/product/v-slider-diy-camera-slider/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) for about £260 with a motor:

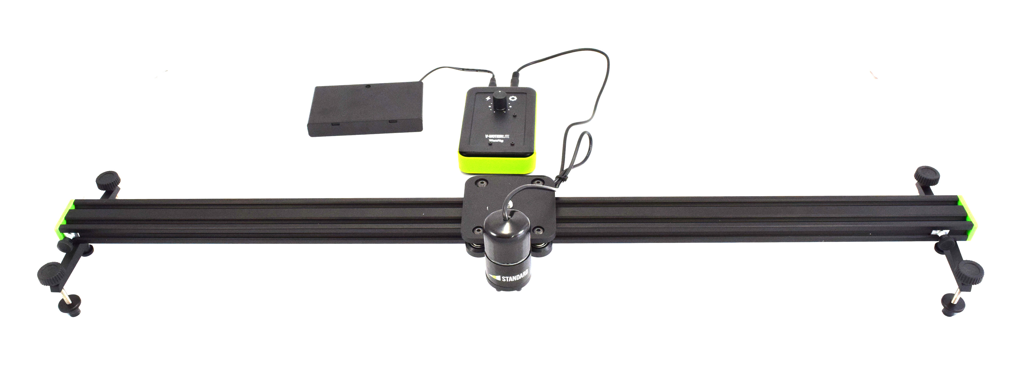
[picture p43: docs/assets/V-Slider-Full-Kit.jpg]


V-Slot sell a simple [linear actuator](http://vslot-europe.com/home/123-v-slot-linear-actuator-bundle-belt-driven-1meter-150cm.html) based on one 2040 aluminium extrusion rail, and a Nema 17 motor for €120:
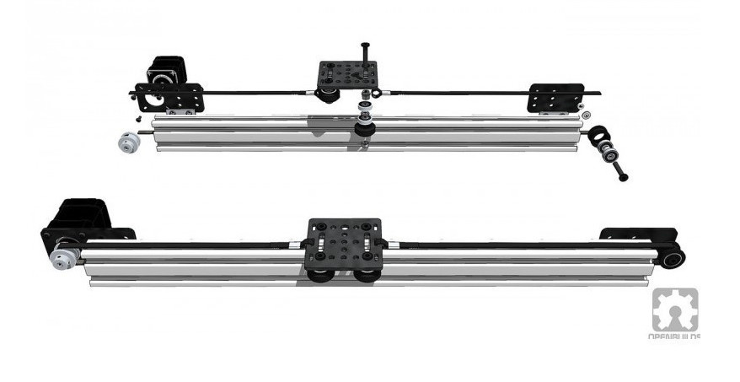
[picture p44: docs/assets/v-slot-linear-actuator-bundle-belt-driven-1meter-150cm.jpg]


This mounts the motor at one end of the rail and uses a loop of timing belt to move the gantry.

#### DIY sliders
There are several Fab Academy slider projects, e.g.:
* Barcelona 2018: [Week 15: Machine design - Group4 Machine Design @FabAcademy](http://barcelonamachines.fabcloud.io/group4/2018/05/14/week15-machine-design.html)  / [Week 15 - Machine Design - Part II](http://fab.academany.org/2018/labs/barcelona/students/oscar-gonzalezfernandez//2018/05/16/Week-15-Machine-Design-Part-II.html) (Using a DRV8825 stepper motor driver
* Aachen 2018: [Fab Lab Aachen @ Fab Academy](http://fab.academany.org/2018/labs/fablabaachen/groupProjects/machine.html)

And some on Instructables, such as: [Make an Arduino Controlled Motorized Camera Slider!: 13 Steps (with Pictures)](https://www.instructables.com/id/Make-a-Motorized-Camera-Slider/). This one adapts a non-motorised rail, using a Nema 17 stepper and ‘A4988 Compatible’ driver board.

There’s also [this one](https://howtomechatronics.com/tutorials/arduino/diy-motorized-camera-slider-pan-tilt-head-project/) that uses three Nema 17 steppers (and three A4988 driver boards) for sliding, panning and tilting. It’s based on a frame of copper plumbing pipes and MDF brackets.

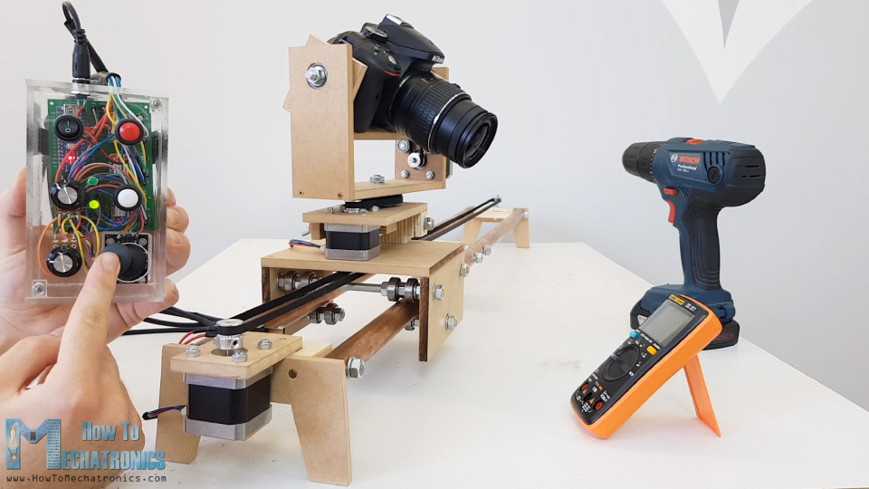
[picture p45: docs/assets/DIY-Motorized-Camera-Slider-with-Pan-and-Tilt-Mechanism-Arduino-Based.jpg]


Adafruit have a [lovely slider](https://learn.adafruit.com/motorized-camera-slider-mk3) with nice 3D printed parts, and great assembly documentation. It mounts the motor at one end and attaches a loop of GT2 timing belt to the gantry. They use the [Adafruit Motor/Stepper/Servo Shield for Arduino v2 Kit](https://www.adafruit.com/product/1438) driver board

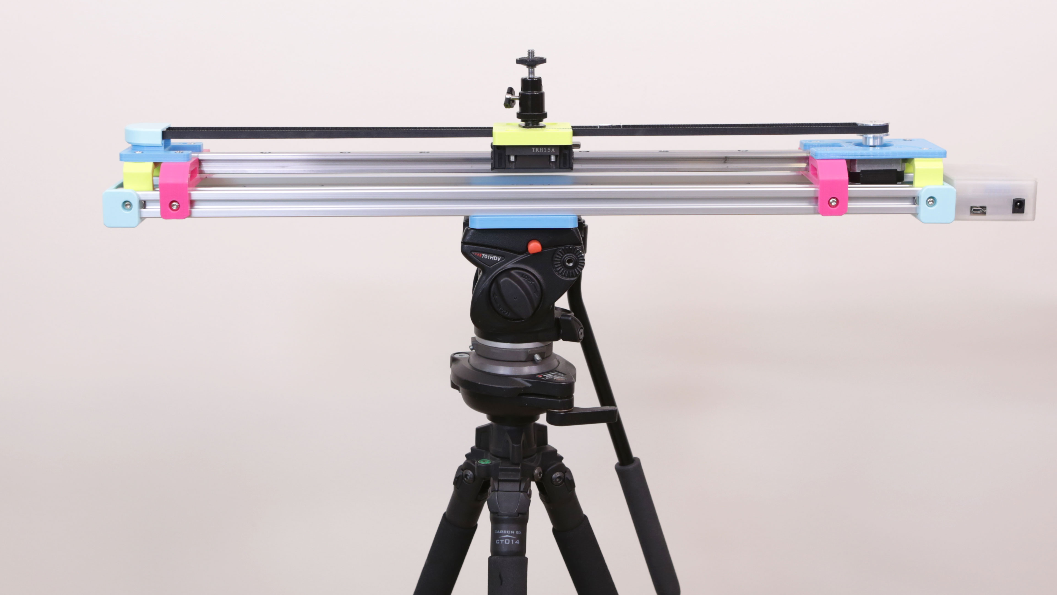
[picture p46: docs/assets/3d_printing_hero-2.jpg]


But it uses this definitely-not-standardised [sliding ball-bearing rail and platform](https://www.adafruit.com/product/1866) which will set you back $55 . That’s in addition to the two lengths of 2020 extrusion that are still needed for the main frame. Possibly money well-spent, but I’d rather stick to standard components.

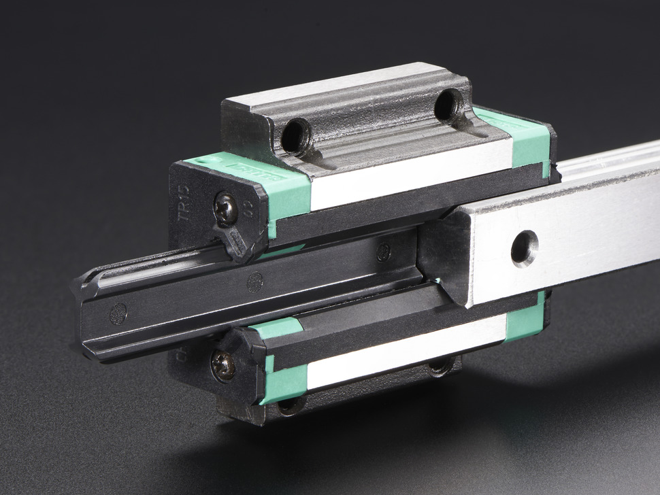
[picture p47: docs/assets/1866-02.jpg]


This is a pretty good tutorial on the electronics side (and includes functionality to trigger the shutter release from the Arduino as well as handling the slider itself): [Motion Control With Arduino: Motorising a Camera Slider](https://computers.tutsplus.com/tutorials/motion-control-with-arduino-motorising-a-camera-slider--cms-21539)

Next: [Problems to be Solved &rarr;](../getting-started-2-problems-to-solve/)

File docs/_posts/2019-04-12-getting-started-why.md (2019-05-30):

---
permalink: getting-started-why/
title: Why am I doing this, and what am I trying to make?
date: 2019-04-12
author: Andrew
layout: page
sort_id: 10
sort_tag: v1_getting_started
---

## Introduction
A camera slider is a simple machine that smoothly moves a still or video camera along a track, sometimes rotating the camera so it remains targeted at the same spot. It allows you to create more interesting and revealing time lapses, but also more interesting footage of still objects that can be used as part of a larger video project. For these reasons they are useful tools for makers who want to document processes, or show off final projects in videos.

I would like to make one myself. Right now, there’s almost nothing I know about how to do it, so these notes serve as a document of what I’m learning.

### Why am I doing this?
* A slider is a good candidate for assembly with 3D-printed parts. I’ve done very little 3D printing, so this is a good excuse for me to learn more about it.
* Many makers photograph their projects poorly. There is a great deal of skill involved, but having the right kit helps too. Along with some good documentation on how to use it, a slider could be helpful here.
* More broadly, I can foresee a set of fab-able photography tools that together could be adopted more broadly by labs and other maker spaces that would solve more photography and video problems: lighting, backdrops, stands, sound recording, etc.
* One of the things that appeals to me about the fablab ethos is the culture of sharing and developing a common set of tools. A good camera slider could be a useful addition to the suite.
* There are many commercial sliders available, but they tend to be expensive (and of course, not made by you or me). There are many DIY versions, but they are often of indeterminate quality, or poorly documented.
* Finally, just because I got it into my head.

### My aims for this slider

* Smooth, controllable motion
* Flexible in the kinds of cameras that can be supported (e.g. phone to full-frame SLR)
* Made using standardised, widely-available components and materials
* Manufacturable in a standard fablab or typical makerspace
* Significantly cheaper to make that a decent quality commercial alternative
* Able to shoot both realtime video (eg. traversing 1m in 10 seconds) and timelapse photos (eg. traversing 1m in 1 or 10 hours)
* Quiet, so if used for video, there is no discernible machine noise recorded

### Feature list

There are many features I would like, but not all are achievable in version 1, so I’ve ordered these by importance, with a proposed cut-off line for features that could be pushed back to version 2.

#### Version 1 prototype / proof-of-concept
* Controlled by commercial Arduino board and motor driver boards
* 50 cm traverse for compactness and affordability
* On-machine controls
* Speed can be adjusted for realtime video or long-duration time-lapse

#### Version 2 improvements or additional features
* Rotating camera mount, so subject can be tracked throughout the traverse. (This may well be critical enough that it should go in version 1)
* Uses a DIY controller board, possibly with integrated microcontroller (so all control is handled by one integrated, fab-able board, along the lines of the Satshakit series: [GitHub - satstep/satstep6600: Open source & fabbable stepper driver based on TB6600.](https://github.com/satstep/satstep6600))
* 1 m traverse (or a design that allows for different lengths to be used or even swapped out)
* Controlled wirelessly using phone or computer
* Adjustable feet to compensate for uneven surfaces and dampen vibration
* Power from portable supply

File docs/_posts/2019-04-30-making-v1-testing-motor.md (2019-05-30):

---
permalink: making-v1-testing-motor/
title: Testing the motor and driver
date: 2019-04-30
author: Andrew
layout: page
sort_id: 40
sort_tag: v1_making
---

Having never used a stepper motor before, I started by trying to get my head around how these can be controlled via Arduino.

## Driver board pinout

These boards have headers for connection to a breadboard (or carrier board). Unfortunately the pins are labelled on the underside, so it’s difficult to see what’s going on once you have it installed on a breadboard. In the end, I just connected wires directly from my Arduino and power supply to the male headers on the underside of the board.

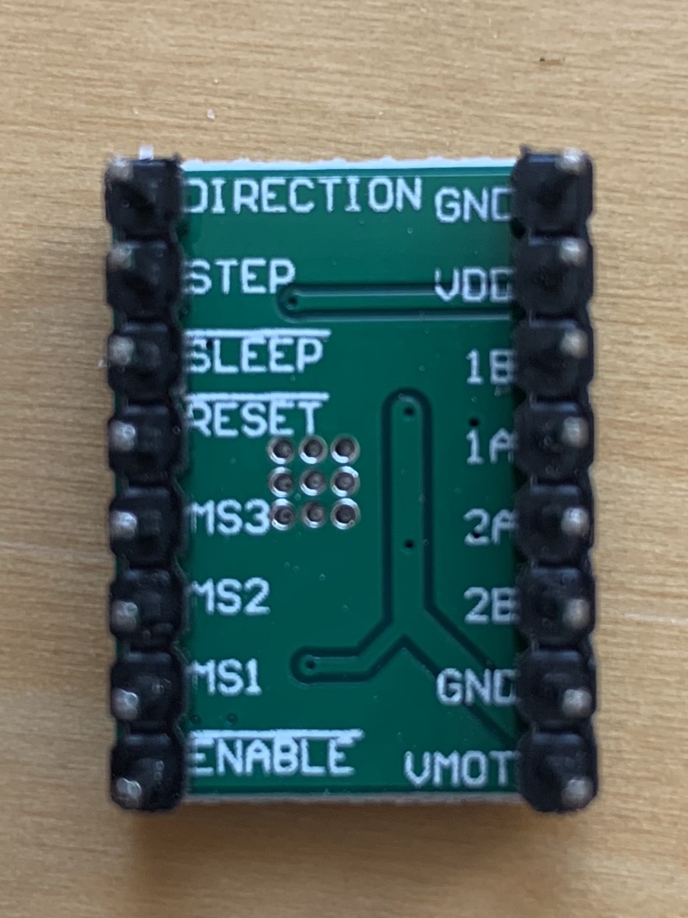
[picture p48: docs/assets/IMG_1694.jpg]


SparkFun’s [Big Easy Driver stepper motor driver](http://www.schmalzhaus.com/BigEasyDriver/index.html)(based on the same chip) has some nice documentation, so I wanted to use that to start experimenting with my motor. However the header pin arrangement and labelling on their board is slightly different, so I had to map one to the other. It was mostly pretty easy, except for the voltage pins (VDD and VMOT). So I had to do some digging on those:

The BigEasyDriver has a pin labelled M+:
> M+ : This is the power input to the Easy Driver. Connect this to the positive power supply lead. This should be a 6V to 30V, 3A (or more) power supply that is clean (low ripple).

The datasheet has a V pin called VBB (2 in fact, which are shorted with a large 100uF capacitor). This is the “Load Supply Voltage“, rated up to 35 V. So I think VBB maps to M+. And on my board, the largest capacitor is near the VMOT pin, so I think this is the equivalent

The BigEasyDriver also has a pin labelled VCC:
> VCC : This is an OUTPUT pin that will provide either 5V (default) or 3.3V from the voltage regulator, at a small amount of current (say 50mA - depends on input voltage) to power a circuit that you may need powered.

On the datasheet, I think this maps to the pin VDD, “Logic Supply Voltage“ (rated at –0.3 to 5.5 V). And I think this should map to VDD on my board.

The result:

### Left side –  viewed from the bottom – reading top to bottom

| DIRECTION | This needs to be a 0V to 5V (or 0V to 3.3V if you’ve set your Big Easy Driver up that way) digital signal. The level if this signal (high/low) is sampled on each rising edge of STEP to determine which direction to take the step (or microstep). |
|   STEP    |                               This needs to be a 0V to 5V (or 0V to 3.3V if you’ve set your Big Easy Driver that way) digital signal. Each rising edge of this signal will cause one step (or microstep) to be taken.                               |
|   SLEEP   |                                                       This normally high input signal will minimize power consumption by disabling internal circuitry and the output drivers when pulled low.                                                       |
|   RESET   |                                                                 This normally high input signal will reset the internal translator and disable all output drivers when pulled low.                                                                  |
|    MS3    |                                                                                                These digital inputs control the microstepping mode.                                                                                                 |
|    MS2    |                                                                                                These digital inputs control the microstepping mode.                                                                                                 |
|    MS1    |                                                                                                These digital inputs control the microstepping mode.                                                                                                 |
|  ENABLE   |                                                                                      This normally low input signal will disable all outputs when pulled high.                                                                                      |

### Right side –  viewed from the bottom – reading top to bottom)

|   GND    | There are three GND (Ground) pins on the Big Easy Driver. They are all connected together inside the board. Connect the negative side of your power supply; as well as from any other boards you are using to drive the Easy Driver to one or more of the GND pins. |
| **VDD**  |                          This is an OUTPUT pin that will provide either 5V (default) or 3.3V from the voltage regulator; at a small amount of current (say 50mA - depends on input voltage) to power a circuit that you may need powered.                           |
|    1B    |                         These are the motor connections. See below diagrams for how to hook these up. A and B are the two coils of the motor and can swap the two wires for a given coil (it will just reverse the direction of the motor).                         |
|    1A    |                                                                                                                             (as above)                                                                                                                              |
|    2A    |                                                                                                                             (as above)                                                                                                                              |
|    2B    |                                                                                                                             (as above)                                                                                                                              |
|   GND    |                                                                                                                           (as GND above)                                                                                                                            |
| **VMOT** |                                          M+ : This is the power input to the Easy Driver. Connect this to the positive power supply lead. This should be a 6V to 30V 3A (or more) power supply that is clean (low ripple).                                          |

## Safety

I’ve heard that it’s quite easy to fry a stepper driver (or even the motor itself). I’m not clear why, but it seems there are a few common causes:

### Intermittent connections

 One possible cause is disconnecting the motor (intermittently) while still providing power to the board. From the BigEasyDriver instructions, referring to the voltage out pins - 1A, 1B, 2A, 2B:

> Make CERTAIN that this connection to the motor is solid, and NOT through a connector that has any chance of intermittent contact (which will fry the motor driver chip).

And from [In-Depth: Interface A4988 Stepper Motor Driver Module with Arduino](https://lastminuteengineers.com/a4988-stepper-motor-driver-arduino-tutorial/):

> WARNING
> Connecting or disconnecting a stepper motor while the driver is powered can destroy the driver.

### Voltage spikes

From [In-Depth: Interface A4988 Stepper Motor Driver Module with Arduino](https://lastminuteengineers.com/a4988-stepper-motor-driver-arduino-tutorial/):

> According to datasheet, the motor supply requires appropriate decoupling capacitor close to the board, capable of sustaining 4A.
> WARNING
> This driver has low-ESR ceramic capacitors on board, which makes it vulnerable to voltage spikes. In some cases, these spikes can exceed the 35V(maximum voltage rating of A4988), potentially permanently damaging the board and even the motor.
> One way to protect the driver from such spikes is to put a large 100µF (at least 47µF) electrolytic capacitor across motor power supply pins.

At the moment, I'm driving the motor from the 12V VIN supply on my Arduino, which I believe has protection against spikes, however, this modification would be easy to implement on a dedicated power supply.

### Allowing the motor to draw too much current

<span class="wip">WIP</span> Here's something I don't fully understand. It's easy to blow an LED by allowing it to draw all the current it can – because it has no/low internal resistance. I don't know if limiting the current to a stepper motor works the same way. 

However, it is possible to limit the curent to the motor to within its safe limit using the trimmer potentiometer on the driver board.

## Adjusting current draw

Many explanations of these driver boards talk about the need to adjust the current draw using the small trimmer potentiometer. My board even came with a tiny screwdriver for just this purpose.

My initial attempts to do this were physically a mess (it's difficult to connect everything up) and the results were difficult to interpret. (Turning the trimmer seemed to affect the current draw in inconsistent ways, with none of the readings making any sense, given the data I do know about the motor, power supply and so on.)

Eventually I found some [good instructions on the Pololu site](https://www.pololu.com/product/1182/faqs):, and a [very good video](https://www.youtube.com/watch?v=89BHS9hfSUk), and I managed to get some sensible readings from my multimeter.

### The process I followed

Determine the amount of current you want to use to run the motor: Mine is 1.68A/phase 

Choose a driver with a max current rating higher than the current you want to use to drive you motor
Then limit the current to below the max rating of the motor. My A4988 driver board is rated at up to 2A per coil

Then, use the current limit calculation for your driver to calculate the appropriate VREF voltage setting . Mine is a Stepstick clone. From [StepStick - RepRap](https://reprap.org/wiki/StepStick):

> To calculate the current, A = VREF / (8 * RS). For a standard stepstick, RS is the rating of the Sense Resistor = 0.2ohm. So A = VREF / 1.6
> To calculate the VREF for a target current, VREF = A * 8 * RS , or A * 1.6 . So, if you wanted 0.8A, VREF = 0.8 * 1.6 = 1.28V

However, RS on my boards is a different value. It’s marked `R100` – ie 0.100Ω, so for these boards 

VREF = A * 8 * RS  
 = 1.68 * 8 * 0.1  
 = 1.344 V

From [StepStick - RepRap](https://reprap.org/wiki/StepStick):
> There is a test point for VREF on the Pololu but it is missing on the Stepstick. Since it is just the wiper of the pot you can measure it there and it is easier as it is a bigger target. I hold the positive meter probe on the shaft of a metal screwdriver so I can see the value while I am turning the pot. Put the negative probe on a ground pin.

* By clipping the positive meter lead to a screwdriver and adjusting the trimmer pot, I can get a range of 0 - 1.12V.  All within the limit of my motor.

### Making use of the 70% current headroom?

As per the A4988 datasheet, on full step mode, the driver only sets the coil current to 70.71%, however, if you use micro-stepping mode, as I intend to, it does use 100% of the current on some steps, so this gives me no room to increase the current more. 

## Simple programs

There are many simple stepper programs that make the motor turn, without the use of libraries or the motor's special modes.

Here's one:

```
/*     Simple Stepper Motor Control Exaple Code  
 *  by Dejan Nedelkovski, www.HowToMechatronics.com
 */
// defines pins numbers
const int stepPin = 3;
const int dirPin = 2;

void setup() {
  // Sets the two pins as Outputs
  pinMode(stepPin,OUTPUT);
  pinMode(dirPin,OUTPUT);
}
void loop() {
  digitalWrite(dirPin,HIGH); // Enables the motor to move in a particular direction
  // Makes 200 pulses for making one full cycle rotation
  for(int x = 0; x < 200; x++) {
    digitalWrite(stepPin,HIGH);
    delayMicroseconds(500);
    digitalWrite(stepPin,LOW);
    delayMicroseconds(500);
  }
  delay(1000); // One second delay

  digitalWrite(dirPin,LOW); //Changes the rotations direction
  // Makes 400 pulses for making two full cycle rotation
  for(int x = 0; x < 400; x++) {
    digitalWrite(stepPin,HIGH);
    delayMicroseconds(500);
    digitalWrite(stepPin,LOW);
    delayMicroseconds(500);
  }
  delay(1000);
}

```

And this demonstrates the most basic functions of the driver chip: to set direction, and speed:

> **Control Spinning Direction**: To control the spinning direction of a motor we set the DIR pin either HIGH or LOW. A HIGH input spins the motor clockwise and a LOW will spin it counterclockwise.
>
> **Control Speed**: The speed of a motor is determined by the frequency of the pulses we send to the STEP pin. The higher the pulses, the faster the motor runs. A pulses is nothing but pulling the output HIGH, waiting a bit then pulling it LOW and waiting again. By changing the delay between two pulses, you change the frequency of those pulses and hence the speed of a motor.

## Initial problems

### Floating RESET pin

Initially, when I tried this code, nothing happened, except a slight grinding noise when I jiggled the board around, or moved my hand close to it. After, some digging, I found [this bit of essential advice](https://lastminuteengineers.com/a4988-stepper-motor-driver-arduino-tutorial/):

> The RST pin is floating. If you are not using the pin, you can connect it to the adjacent SLP/SLEEP pin to bring it high and enable the driver.

Floating pins are a familiar source of unreliable input. If you’ve ever tried to wire up a simple button to an Arduino and had it behave seemingly randomly, you’ve experienced this. In particular, just moving your hand close to the board can be enough to change the voltage on the pin. So I suspected this might be the problem, and sure, enough, when I connected together RESET and SLEEP, my demo Arduino sketch worked fine.

### Adjusting current

As noted above, for some settings of the current trimmer, the motor seemed to move unreliably, or with a lot of noise or vibration. I tried turning the trimmer (I don't know which way is 'up') and that seemed to help.

## AccelStepper Arduino library

Then I went looking for a library that would let me control the motor easily without having to write code to pulse the STEP pin manually. Arduino has a built-in stepper library, but I also found the AccelStepper library, which seems to be more fully-featured, though lacking in much basic documentation beyond the class/function reference, which is not very helpful when you're getting started.

You can install this library, with examples, through the Arduino Library Manager.

Here's the basic sketch to get the motor turning at a set speed:

```
// ConstantSpeed.pde
// -*- mode: C++ -*-
/// \author  Mike McCauley (mikem@airspayce.com)
// Copyright (C) 2009 Mike McCauley
// $Id: ConstantSpeed.pde,v 1.1 2011/01/05 01:51:01 mikem Exp mikem $

#include <AccelStepper.h>

AccelStepper stepper(AccelStepper::FULL2WIRE, 3, 2);

void setup()
{  
   stepper.setMaxSpeed(1000);
   stepper.setSpeed(150);
}

void loop()
{  
   stepper.runSpeed();
}
```

Note the [parameters passed to the constructor function](http://www.airspayce.com/mikem/arduino/AccelStepper/classAccelStepper.html#a3bc75bd6571b98a6177838ca81ac39ab). The default format is:
`AccelStepper stepper;`. By using the format, `AccelStepper stepper(AccelStepper::FULL2WIRE, 3, 2);` I'm specifying a particular kind of motor (perhaps incorrectly...) and setting pin 3 to be the STEP pin, and 2 to be the DIRECTION pin.

There is [some useful explanation here](https://groups.google.com/forum/#!topic/accelstepper/548T1E4tbfo):

> So the first parameter is the interface type, and is one of the types listed (1, 2, 4, 6 or 8), and the parameters after that define the actual pins that are wired up. The examples don't show anything except the default way of accessing the object, without any parameters at all, which maybe doesn't help.
>
> `AccelStepper stepper(1, 3, 2);` is synonymous with `AccelStepper stepper(AccelStepper::DRIVER, 3, 2);` which might make a bit more sense.
>
> The above means that the stepper object is created, interfaced to a hardware stepper motor driver (like a DRV8825) using two wires from arduino pins D3 and D2.
>
> Again looking at the docs, for the constructor, pin1 (defined as D3 in your example) is the step input to the driver and pin2 (defined as D2 in your example) is the direction input to the driver.

## Problems

### Noise and vibration

That worked, but it was super noisy. (I think this is due to the STEP pin being pulsed...) I tried using the micro-step functions and increasing the speed to compensate, however, after turning this up to, I think 6000, my motor stopped working. I ordered some new drivers, which did work, so I can only assume I fried the driver board.

### Stopping the motors using the stop() function

I also tried simulating the effect of the gantry hitting the end-stop switch:

```
void loop()
{  
   stepper.runSpeed();

  // while the button is pressed ...
  while (digitalRead(buttonPin) == HIGH) {
   stepper.stop();
  }  
}   
```

While this worked, I found that after I released the button the motor didn't start properly again, just grinding without moving.

I got around this by not using the  `stepper.stop();` function, and instead putting the `stepper.runSpeed();` function inside a conditional. But it would be good to understand the cause of the problem. <span class="wip">WIP</span>

### Purpose of setMaxSpeed() function

<span class="wip">WIP</span>

I don't know why this is in the example code. If it's made redundant only by the use of the runSpeed() function instead of run(), why is it in the example code?

### FULL2WIRE parameter in AccelStepper constructor

Have I used this incorrectly? My motor does have 4 wires... I think when I set this I may have been confusing the control wires (STEP and DIRECTION) and the motor coil wires.

I wonder if this is causing some of the problems I'm having... <span class="wip">WIP</span>

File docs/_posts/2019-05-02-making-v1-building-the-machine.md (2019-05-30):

---
permalink: making-v1-building-the-machine/
title: Building the mechanism
date: 2019-05-02
author: Andrew
layout: page
sort_id: 42
sort_tag: v1_making
---

I had a few days access to the fablab, so I tried to make as much of the physical hardware as I could so I could work on the motion control software later. One of [my original aims for the project](../getting-started-why/) was to try and learn more about 3D printing, and I was very successful in this aspect. I [modelled the whole assembly in Fusion 360](https://github.com/andrewsleigh/fab-slider/tree/master/3d-parts/v1/assembly) and 3D-printed several iterations of key parts on our Creality CR-10 printer. I had a lot of fun with it.



All the parts mentioned in this posts are in the <a href="https://github.com/andrewsleigh/fab-slider">GitHub repository</a>. Links are included in each section.

## End-caps (<a href="https://github.com/andrewsleigh/fab-slider/tree/master/3d-parts/v1/extrusion-end-caps">GitHub repo</a>)

<script src="https://embed.github.com/view/3d/andrewsleigh/fab-slider/master/3d-parts/v1/extrusion-end-caps/end-cap-3D.stl"></script>

This design requires caps at each end to hold the rails in position, and to act as feet for the whole assembly. This approach is simpler, and more physically sound than many of the other approaches I've seen, which rely on complex 3D-printed parts that fit into the V-slot, or special V-slot right-angle brackets, that introduce more hardware, and with it, cost and instability. 

However, here is one drawback, it requires tapped holes in the ends of the extrusion, which don't come as standard. 

### Tapping holes in the V-slot

The V-slot extrusion has holes in each end, which can be tapped to an M5 thread. Some suppliers (like Ooznest) will do this for you, or you can do it yourself. I thought I would ask them to tap some of the holes and do the rest myself, since I'd like this to be as DIY as possible. 

However, despite having had some experience tapping holes before – and watching some [good videos](https://www.youtube.com/watch?v=r6Ijd9o-C10) – I had limited success. I shattered one tap, leaving it stuck in the hole, and after a little more practice, on my three remaining holes, only did a good job on two of them.  

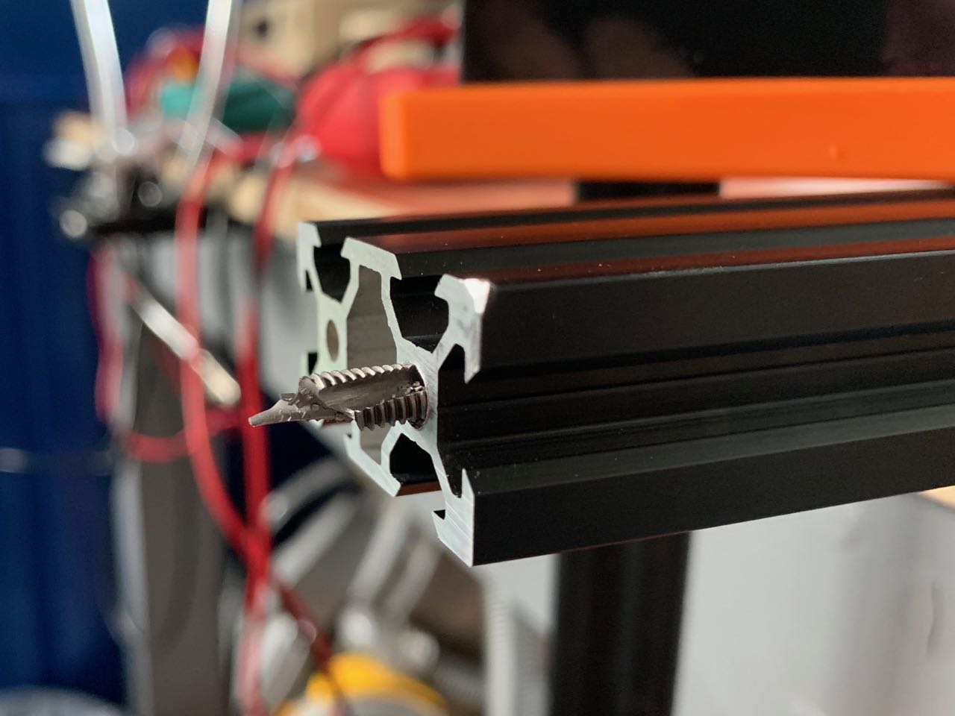
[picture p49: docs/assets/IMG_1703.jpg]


So I ended up using the pre-tapped holes on the business end of the slider, where the motor is mounted, and on the other end, using a combination of some of my tapped holes, and right-angle v-slot brackets to mount the end-cap.

For a future version, I would like to design a mounting system that doesn't rely on tapped holes at all, as there is too much room for error.

## Gantry (<a href="https://github.com/andrewsleigh/fab-slider/tree/master/3d-parts/v1/gantry">GitHub repo</a>)



This is a surprisingly complex part! It needs to perform a few functions:

* Hold a camera (by embedding a 1/4" screw)
* Attach to the timing belt
* Make contact with the end-stop switches at each end of the slider
* Mount onto the wheels which slide in the V-slot.

<script src="https://embed.github.com/view/3d/andrewsleigh/fab-slider/master/3d-parts/v1/gantry/gantry.stl"></script>

The camera screw needs to be captured inside the gantry in some way, so I added a small screw-in plate, which captures it from the underside. 

The belt is attached to the gantry by two bolts that protrude underneath it. Each end of the belt can be wrapped around one of the belts and secured with a cable tie. This seems to work pretty well in practice. 

There are two more bolt-mounting holes for bolts that protrude underneath the gentry  and should hit the end-stops at each end of the traverse. I suspect I actually only ned one though. This is something that needs to be worked out when I'm working on the end-stop code.

### Wheels

I bought [some relatively cheep wheels](https://www.amazon.co.uk/BIQU-Printer-Plastic-Bearings-Passive/dp/B06X9Q9Y8V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), which are OK, though don't turn as easily as I expected. However, this is my first experience woking with bearings, so I don't know what I should expect. 

### Wheel adjustment

I mounted one pair of wheels through circular holes in the gantry, and the other set through elongated slots, perpendicular to the rails, to allow the wheel spacing to be adjusted slightly. 

This worked OK in the 3D printed gantry (less so in the laser-cut acrylic version, where there is less friction between the nut and the gantry). It also made it possible to mount and demount the gantry even when the end-caps are fitted, and it can't be slid off an end.

### Washers

Initially, I used washers on the wheel assembly – it's just a convention that I've got used to, to add washers to enable free rotation of parts against a tightened nut. But of course, in this assembly, the bearing itself is designed to be held firm in the assembly at the centre, but to rotate freely on the outside. And I found the washers were interfering with this, so I removed them.

## Motor backet (<a href="https://github.com/andrewsleigh/fab-slider/tree/master/3d-parts/v1/motor-bracket">GitHub repo</a>)

<script src="https://embed.github.com/view/3d/andrewsleigh/fab-slider/master/3d-parts/v1/motor-bracket/motor-bracket.stl"></script>

This was a simple part to design. It just needs to hold the motor at 90&deg; against the end of the slider rails.



However, my current design is attached to the rails by bolting through the end-cap into the threaded holes in the extrusion. That's a solid design, but perhaps less easy for others to replicate. So for a future design, it would be good to think about an alternative approach that doesn't relay on these threaded holes.

## End-stops (<a href="https://github.com/andrewsleigh/fab-slider/tree/master/3d-parts/v1/endstop-clip">GitHub repo</a>)

I already had some end-stop switches left over from a previous project. I just had to find a way to mount them. They do have tiny holes, that perhaps might take an M2 bolt, but I didn't have any of those, so instead, found a <a href="https://www.thingiverse.com/thing:2204123">nice clip on Thingiverse</a>.

### End-stop wiring

My switch wiring is currently way more complex than it likely needs to be, but I thought it was worth wiring the switches for maximum flexibility at this stage, even if I make things simpler later one. 

The switches have 3 contacts, labelled:

* NO –  Normally Open
* NC – Normally Closed
* C – COM/Common 

An end-stop should be activated when it is pressed, but ideally, it should also prevent motion of the gantry if there is a defect with the switch, for example, one of the wires is cut, or the contact is dirty. So its default behaviour (no continuous circuit between NO and C) should be 'stop movement'.  This should also be the behaviour when the switch is pressed (continuous circuit between NC and C; no continuous circuit between NO and C). And when the switch is open (continuous circuit between NO and C), and the switch is receiving current, the behaviour should be 'allow movement'.

<a href="https://reprap.org/wiki/Mechanical_Endstop">This page</a> explains it well:

>  You want a normally closed (NC) switch. Meaning you need a switch which connects two poles when not triggered.
> ...
> When the switch is off, it connects signal to ground. When the switch is triggered, the ground connection is cut and the signal is connected to 5v through the pull up resistor.

So I need to account for this in both hardware and software:

* Wire up the NO and C pins to signal (Arduino digital input) and GND respectively
* Set the Arduino digital input pin to use the internal pull-up resistor, so that it stays high until the switch is pressed

<span class="wip">WIP</span> I need to play with this in code, and also test out what happens if the switch is just disconnected. 

### Cable clips

I'm running wires from the far end of the slider down towards the  microcontroller board, so I wanted some way of keeping the cables tidy and out of the way. 

Fortunately, Thingiverse has plenty of solutions for this problem, so I printed a few V-slot cable clips that do the job nicely. I used these <a href="www.thingiverse.com/thing:2676595">V-Slot Cable Clips</a>.

## Stepper Driver Arduino shield  (<a href="https://github.com/andrewsleigh/fab-slider/tree/master/boards/driver-arduino-shield">GitHub repo</a>)

At this stage, I'm not thinking too much about how the electronics will be housed. But I got tired of the mess of jumper wires in my tests, nd I'm also thinking ahead to a slightly more integrated solution, so I quickly designed a simple Arduino shield in Eagle to mount my stepper driver, provide an easy connection point for the motor, as well as headers for end-stop switches, and some analogue inputs that I think I might need. 

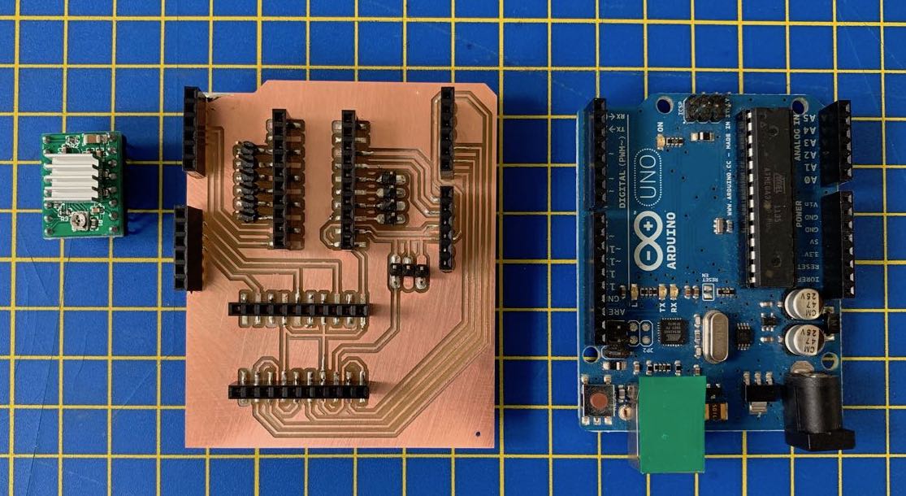
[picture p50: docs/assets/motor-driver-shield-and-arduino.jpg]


This board is basically just headers. And I think I may have already made some mistakes (in the wiring of the end-stop connection headers), so it's unlikely to last in this form for long. 

<span class="wip">WIP</span> I'm pretty sure the end-stop switch headers are incorrectly routed on this board. I should confirm it either way.

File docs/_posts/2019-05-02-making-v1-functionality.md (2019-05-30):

---
permalink: making-v1-functionality/
title: Basic functionality
date: 2019-05-02
author: Andrew
layout: page
sort_id: 41
sort_tag: v1_making
---

I've started to think about the functions needed for the slider to work well, and how these should be implemented in hardware and software.

<hr/>

**Update 2019-05-11:** as a [later post details](../coding-state-machine/), I went a long way down the path of building this: designing a system that would take in all these inputs, and writing code to handle all the events, both intended and unintended. After playing with it, I decided it was too complex, so simplified this considerably. 

<hr/>

## On startup

### Find ends

* Move to one end til you hit switch, then pull back a little. Set `endPoint1`
* Do the same for the other end - `endPoint2`

Hardware controls:

* Maybe nothing - just does this when you connect power
* Or perhaps a reset button to send it to its config state (which just disconnects/reconnects power…)
* Or maybe there should be a ‘setup’ button. So any motion is triggered deliberately.

### Set start and end positions - optional (could just use the two ends)

* User moves gantry to desired starting point - sets `startPoint`
* User moves gantry to desired end point - sets `endPoint`

Hardware controls:

* A button for each
* Plus LED/on-screen feedback?

### Set video or time-lapse mode

* Switch between high- or low-speed ranges
* Timelapse mode could be quite jerky really - maybe better for photos…

Hardware controls:

* Switch

### Set speed

* Vary speed continuously across a range, 

Hardware controls: 

* Potentiometer could work. Want to read this value once, then ignore input for the rest of the program
* Ideally with some feedback (even just markings on a dial)
* Rotary encoder could also work, but would need visual feedback, e.g. 7-segment display or OLED module

### Pause and reset buttons

Could be handled with a mode, set in the code. One button press turns it into pause mode, stopping movement, another button press cancels everything….

### Power off or reset power

To Arduino etc.

## While running

* Cancel/reset?
* Pause?
* Should speed control have an effect if used when it's running, or should this be isolated to avoid unintentional changes

## Other control options

Some other projects use Bluetooth or phone apps. This might introduce some complexity, but reduce the need for physical controls.

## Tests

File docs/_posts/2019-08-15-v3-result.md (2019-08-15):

---
permalink: v3-result/
title: Finished — for now
date: 2019-08-15
author: Andrew
layout: page
sort_id: 95
sort_tag: v2_result
---

I've got this version of the slider to a pretty good state. There are improvements I'd like ot make, but for now, I'd like to tackle something else.

I've shot some test videos—see the sample clips below—and plan to do some timelapses soon. 

<div class="video-responsive">
<iframe width="800" height="450" src="https://www.youtube.com/embed/jfUBC_XnyGQ" frameborder="0" allow="accelerometer; autoplay; encrypted-media; gyroscope; picture-in-picture" allowfullscreen></iframe>
</div>

In the meantime, here are some beauty shots (<a href="https://github.com/andrewsleigh/fab-slider/tree/master/images">all photos in the repo</a>). If you're working on a project like this–where you're building something to learn, and documenting the process—I'd love to hear about it.

<h3>Controls and electronics faceplate</h3>

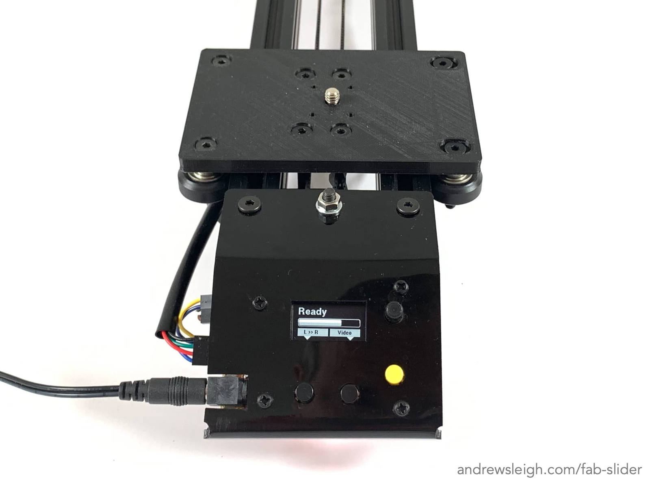
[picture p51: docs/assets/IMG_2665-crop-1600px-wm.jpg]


<h3>Motor end</h3>

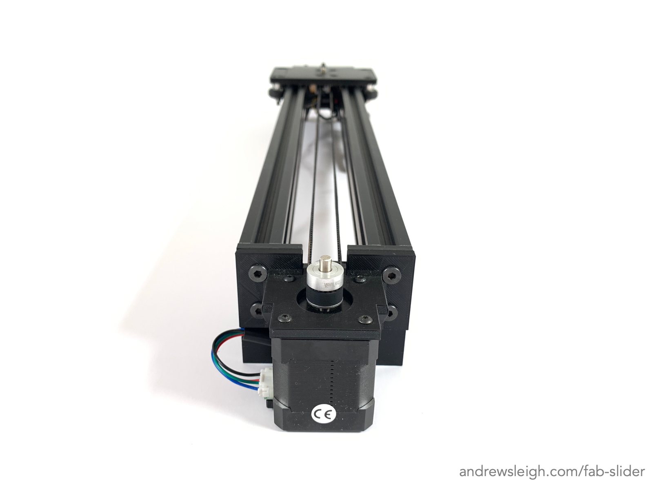
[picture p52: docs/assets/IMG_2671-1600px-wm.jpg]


<h3>Idler pulley and endstop</h3>

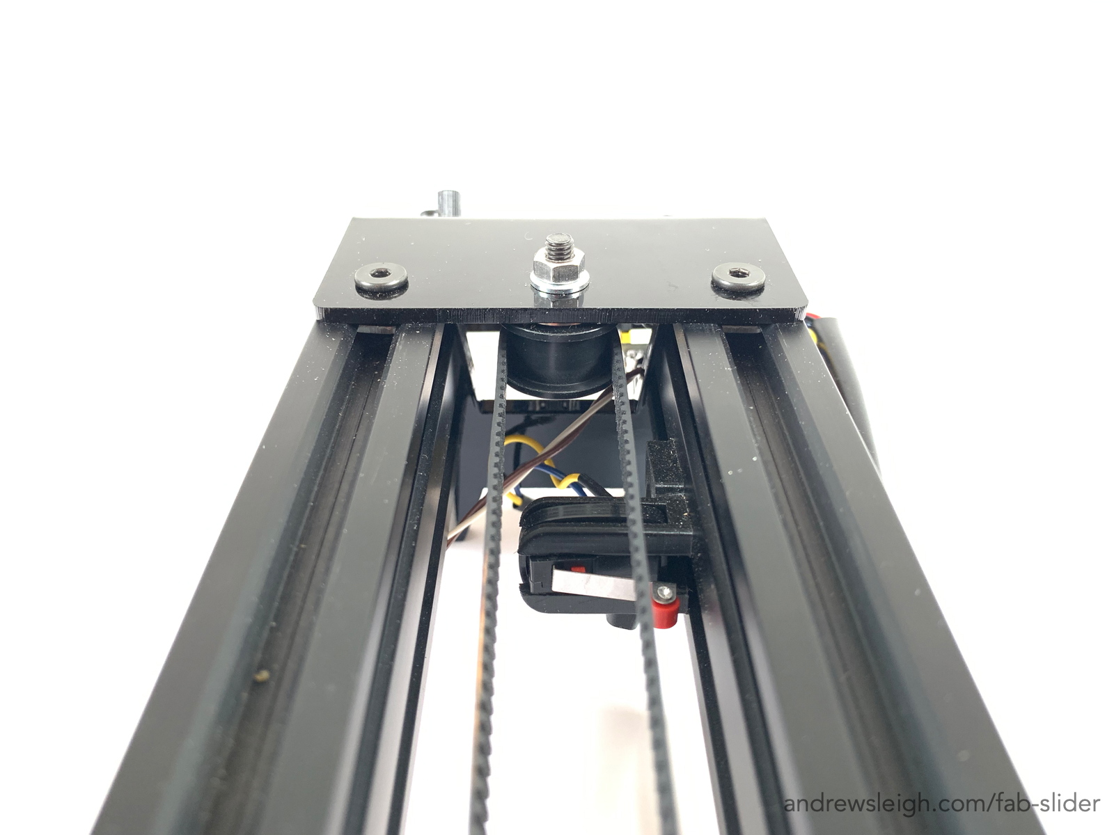
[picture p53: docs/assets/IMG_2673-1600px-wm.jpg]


<h3>With vertical mounting legs attached</h3>

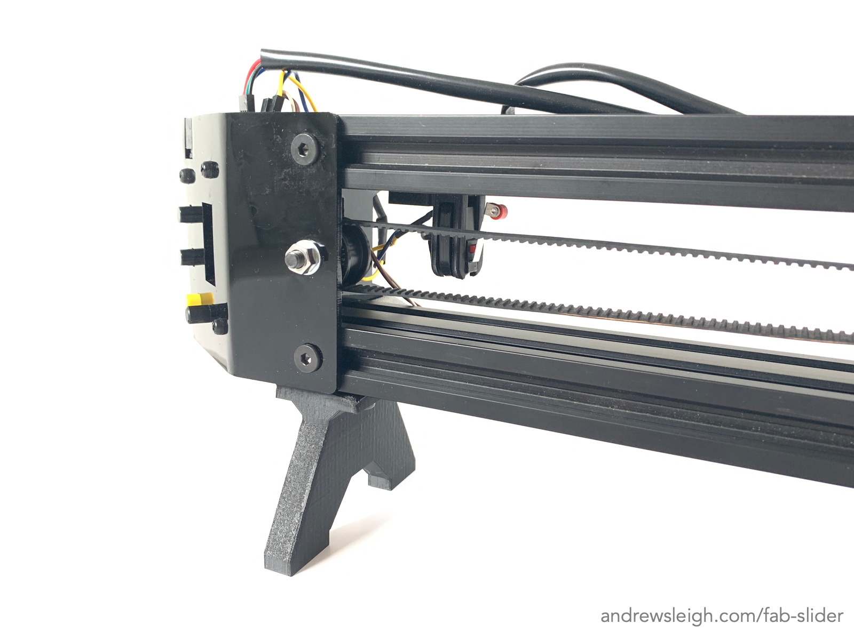
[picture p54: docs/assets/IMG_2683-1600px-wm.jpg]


<h3>Underside of the gantry</h3>

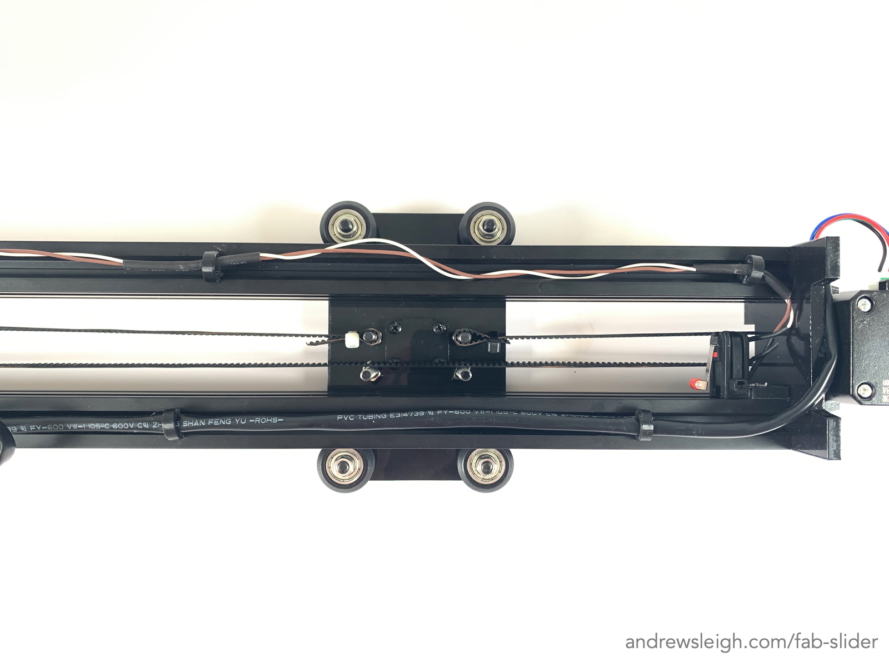
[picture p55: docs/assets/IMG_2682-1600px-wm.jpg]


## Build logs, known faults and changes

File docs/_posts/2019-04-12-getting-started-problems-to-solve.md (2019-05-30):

---
permalink: getting-started-problems-to-solve/
title: Problems already I know I need to solve
date: 2019-04-12
author: Andrew
layout: page
sort_id: 20
sort_tag: v1_getting_started
---

I assume there will be all sorts of problems I need to solve in order to make this. At this stage, these are the ones I can think of.

### Handling different speeds
Will the same motor be able to handle both kinds of usage?

The [Ratrig V-Slider DIY Camera Slider kit](https://ooznest.co.uk/product/v-slider-diy-camera-slider/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) comes with 3 options for motors:

> THE V-MOTION LITE IS AVAILABLE WITH THREE DIFFERENT MOTOR OPTIONS:  
> Timelapse motor – motion is almost unnoticeable in real time  
> Top speed: 1 meter in 18 minutes (1 RPM)  
> Lowest speed: 1 meter in 3 hours  
> Max. Power consumption: 0.09A  
>   
> Standard motor – adequate for timelapses in its slowest setting, adequate for real time action in its fastest   
> Top speed: 1 meter in 38 seconds (28 RPM)  
> Lowest speed: 1 meter in 9 minutes  
> Max. Power consumption: 0.15A  
>   
> Fast motor – great range of speeds for real time action.   
> Top speed: 1 meter in 18 seconds (57 RPM)  
> Lowest speed: 1 meter in 3 minutes  
> Max. Power consumption: 0.29A  

WIP: This needs more research

### Tracking the subject
I was thinking this would need a second motor mounted on the camera gantry itself, but it looks like the commercial models use an adjustable rod mounted to the rails which is mechanically fixed to the granary and rotates it automatically across the traverse.

See for example, [this commercial model](https://www.amazon.co.uk/Motorized-centimeter-Time-lapse-Camecord-Photography/dp/B07D55FZFW?ref_=fsclp_pl_dp_8) (which seems like one of many Chinese clones):

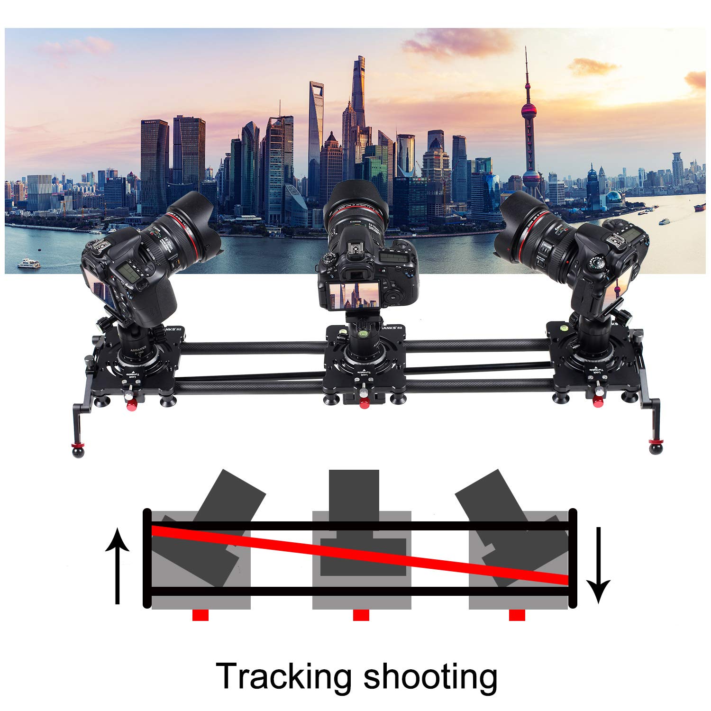
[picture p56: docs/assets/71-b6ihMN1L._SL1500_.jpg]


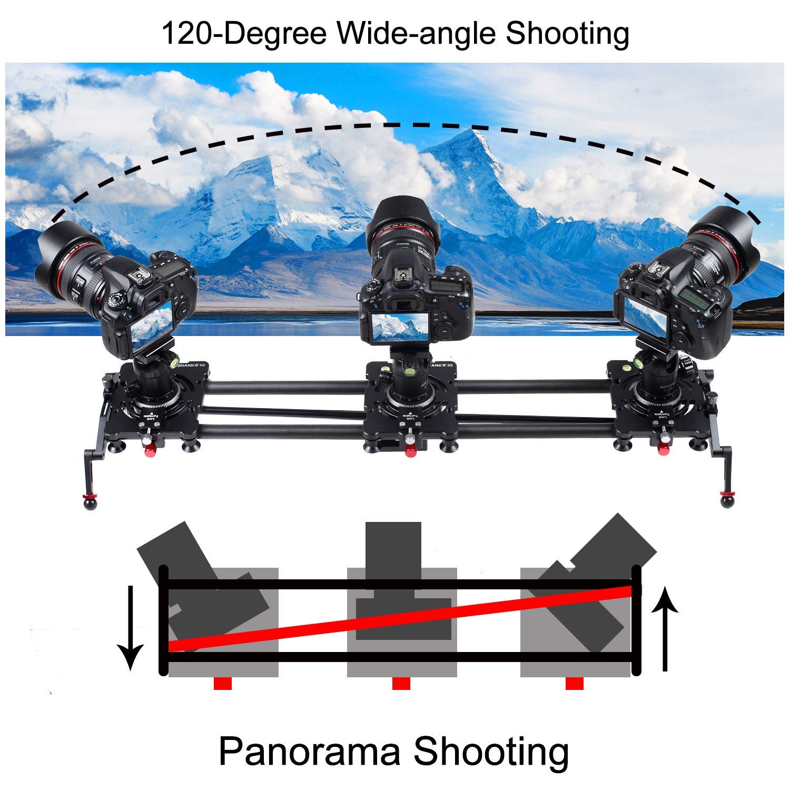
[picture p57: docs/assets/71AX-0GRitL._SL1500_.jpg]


The central rod is attached in a swivel mount to the camera gantry. The rod ends can be moved to any position on each end of the rail. By pulling one side of the gantry forward or back, it rotates the whole gantry.

In the picture below (1) shows how the rod is adjusted, (7) shows how the rod interfaces with the gantry.

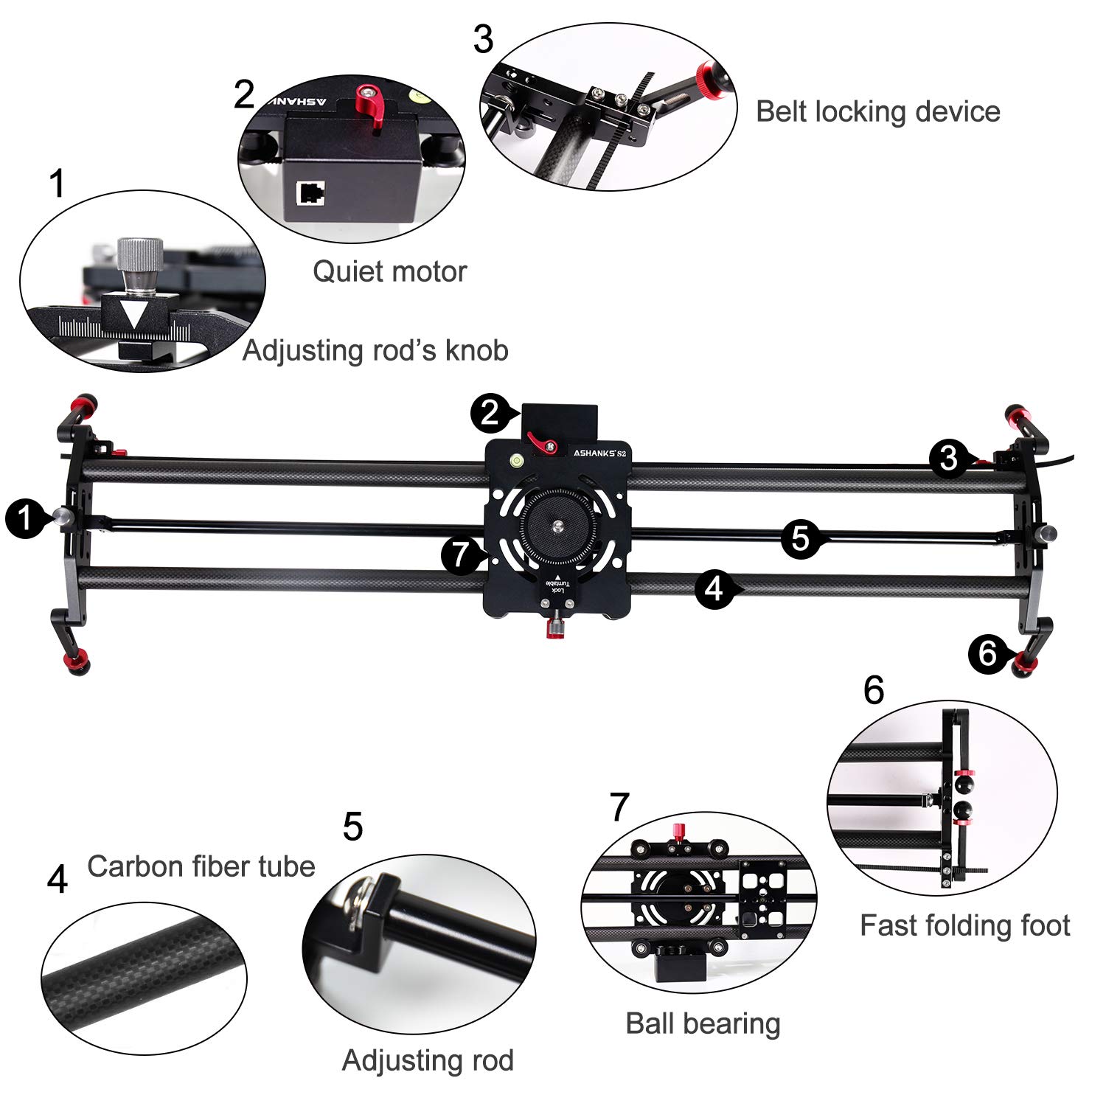
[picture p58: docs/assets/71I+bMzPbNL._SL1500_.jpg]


I imagine you could set the amount of rotation quite easily by hand, by moving the camera to each end of the rail, and adjusting it so that it remains locked on the subject. (Or otherwise, if you want what they call ‘panorama shooting’).

This passive mechanical method would certainly save on complexity if I could make something similar work.

WIP: I think for version 1 I might just put this whole problem aside and have a non-rotating gantry

### Synchronising time-lapse shutter release with motion

From this review on a commercial slider:  <https://www.amazon.co.uk/gp/customer-reviews/RDGLTSU4YIVCB/ref=cm_cr_dp_d_rvw_ttl?ie=UTF8&ASIN=B07BMLD4N4>

> On the timelapse setting, if you set a pause of, say, 2, seconds, it stops for 2 seconds, and then takes the picture at the point it starts moving again. This is a little insane. It needs to stop, take the picture at the *start* of the 2s gap, and then move. It must be still for the whole duration of the picture, obviously.

It sounds like this slider also lets you control the shutter release on the camera. Which could be a nice feature, but is more than I'm trying to do here. Nevertheless, it might be important to try and synchronise shutter release with points when the gantry is stationary – if indeed there are any with the kind of motion control I end up using.

<span class="wip">WIP</span> I'm going to leave this until I have something built.

### Adjusting the gantry so it slides well on the rails

The [Ratrig V-Slider DIY Camera Slider kit](https://ooznest.co.uk/product/v-slider-diy-camera-slider/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) solves this problem by mounting the gantry with eccentric spacers – shims with off-centre holes that can be rotated to position the hole (and therefore the wheel) differently. Too loose a fit and the gantry will be unstable, too tight and there may be too much friction. Either problem could result in jerky movement.

A common solution in furniture design is to mount fixings into slots. This might be a simpler method, needing fewer specialised parts, but is also less finely adjustable.

### Providing user controls and feedback

<span class="wip">WIP</span>. I'll need some sort of controls, but I'm not quite sure what yet.

### Stopping the motor when the slider reaches the end of the rail.

<span class="wip">WIP</span>. I'll need some way of letting the system know when the gantry has got to the end of the rails, so it can be stopped safely.

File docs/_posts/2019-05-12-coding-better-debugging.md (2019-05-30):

---
permalink: coding-better-debugging/
title: Better debugging with the serial monitor
date: 2019-05-12
author: Andrew
layout: page
sort_id: 52
sort_tag: v1_code
---

Up until now, my approach to debugging has just been to litter my code with `Serial.println()` statements that print some input value to the serial monitor, scrolling on for eternity. They're quick to implement, and better than nothing, but I find them messy, easy to get wrong (and give misleading information), and for a project of any complexity, they quickly become confusing to interpret.

SO for this project I've tried to be more methodical, and I'm trying a few approaches out.

## Conditional debugging

Because I'm turning a motor, timing is important. I can't have an interruption every time some data has to be sent to the serial monitor. So I want debugging that i can easily switch off when I'm not using it. 

I found some useful resources on the Arduino forum that make use of  __preprocessors__ in C to do just this:

* <https://forum.arduino.cc/index.php?topic=215334.msg1576067#msg1576067>
* <https://forum.arduino.cc/index.php?topic=46900.0>

There's a nice explanation of these preprocessor keywords here: <https://community.arduboy.com/t/purpose-of-ifndef-and-define/3592/2>

> `#define` defines a word to mean something else.
> E.g. `#define FIVE 5` would result in all instances of FIVE being replaced with 5.
>
> `#if` tests if a condition is true.
> `#else` provides an alternative case for an `#if`, in case it is not true.
> `#endif` ends an `#if`
>
> `#ifdef` tests if a word is defined and `#ifndef` does the opposite - it tests if a word has not been defined.

So at the top of my file, I can include a line like: 

```
#define DEBUG
```

Then include commenting functionality in that only compiles if that line remains uncommented. e.g. 

```
#ifdef DEBUG
// set up string messages
#define DEBUG_PRINT(str)    \
   Serial.print(str); \
   Serial.print(" ------ ");      \ 
   Serial.print("In ");    \
   Serial.print(__PRETTY_FUNCTION__); \
   Serial.print(", line: ");      \
   Serial.println(__LINE__);     \   
#else
#define DEBUG_PRINT(str) // just leaves an empty definition without serial printing
#endif
```

And liberally sprinkle debug messages throughout my code which (a) can be turned off all at once, and (b) also include useful information about what line they're on, and which function they're inside:

```
// one-off debug message
DEBUG_PRINT("This is a one-off message just placed in to the code")
```

## Consolidating debug and status messages into one place

However, this still leaves debug messages all over my code, and I wanted to consolidate them into one place. 

So I wrote a simple function that neatly prints out all the information I want to know about the system at one time:

```
void printDebugMessages() {
#ifdef DEBUG  
  Serial.println("\n------");
  // machine state
  Serial.print("Current state:         ");
  Serial.println(stateLabels[currentState]);

  // latest error message
  if (errorMessage != "") {
    Serial.print("Message:               ");
    Serial.println(errorMessage);
  }

  // control settings
  Serial.print("Start from left?       ");
  Serial.println(startFromLeft);
  Serial.print("Use time-lapse mode?   ");
  Serial.println(isTimelapseSpeed);
  Serial.print("Speed:                 ");
  Serial.println(traverseSpeed);
#endif
}
```

This prints out to the serial monitor like so:

```
------
Current state:         INIT
Message:               Finished traverse
Start from left?       1
Use time-lapse mode?   0
Speed:                 2017
```

I can call that function either from a non-blocking timer that runs inside the main `loop()` and prints messages every couple of seconds:

```
#ifdef DEBUG_TIMER
  if (millis() > debugTimeNow + debugRefreshPeriod) {
    debugTimeNow = millis();
    printDebugMessages();
  }
#endif
```

Or at any other point, for example, every time there is a transition to a new state. 

```
switch (currentState) {
  case INIT:
    
    #ifdef DEBUG_STATE_CHANGE
      printDebugMessages();
    #endif
  
    // do the other INIT state stuff
    // ...
    
  // ...
}  

```

Update: in [later versions](https://github.com/andrewsleigh/fab-slider/tree/master/arduino-code/v1/camera_slider_v1) I added a check for the state change variant to see if the machine has just entered a new state. If so, a message is printed (and the new state flag cleared), otherwise, not. This avoids the status messages being endlessly repeated as the code loops around around state.

For these two variants to work (and to be able to switch them on and off independently) I created a couple more definitions:

```
// comment these out to remove debugging
#define DEBUG // needed for all debugging
#define DEBUG_TIMER // for messages that print every few seconds
#define DEBUG_STATE_CHANGE // for messages that print only on a change in the machine state
```

Although the timer variant is non-blocking, it still takes some time for the Arduino to send all that string data to the serial monitor, which interrupts the movement of the motor, so I'm using the state change variant instead.

This solution works well for this project, but is not particularly portable. [Some people recommend creating a debug header file](https://forum.arduino.cc/index.php?topic=46900.msg338652#msg338652) that can be used in all projects. Obviously mine is quite specific to this project, but perhaps a future version could be made more portable.

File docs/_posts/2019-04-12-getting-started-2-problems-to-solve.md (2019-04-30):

---
permalink: getting-started-2-problems-to-solve/
title: Getting Started 2 – Problems to Solve
date: 2019-04-12
author: Andrew
layout: page
sort_id: 20
---

### Handling different speeds
Will the same motor be able to handle both kinds of usage?

The [Ratrig V-Slider DIY Camera Slider kit](https://ooznest.co.uk/product/v-slider-diy-camera-slider/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) comes with 3 options for motors:

> THE V-MOTION LITE IS AVAILABLE WITH THREE DIFFERENT MOTOR OPTIONS:  
> Timelapse motor – motion is almost unnoticeable in real time  
> Top speed: 1 meter in 18 minutes (1 RPM)  
> Lowest speed: 1 meter in 3 hours  
> Max. Power consumption: 0.09A  
>   
> Standard motor – adequate for timelapses in its slowest setting, adequate for real time action in its fastest   
> Top speed: 1 meter in 38 seconds (28 RPM)  
> Lowest speed: 1 meter in 9 minutes  
> Max. Power consumption: 0.15A  
>   
> Fast motor – great range of speeds for real time action.   
> Top speed: 1 meter in 18 seconds (57 RPM)  
> Lowest speed: 1 meter in 3 minutes  
> Max. Power consumption: 0.29A  

WIP: This needs more research

### Tracking the subject
I was thinking this would need a second motor mounted on the camera gantry itself, but it looks like the commercial models use an adjustable rod mounted to the rails which is mechanically fixed to the granary and rotates it automatically across the traverse.

See for example, [this commercial model](https://www.amazon.co.uk/Motorized-centimeter-Time-lapse-Camecord-Photography/dp/B07D55FZFW?ref_=fsclp_pl_dp_8) (which seems like one of many Chinese clones):





The central rod is attached in a swivel mount to the camera gantry. The rod ends can be moved to any position on each end of the rail. By pulling one side of the gantry forward or back, it rotates the whole gantry.

In the picture below (1) shows how the rod is adjusted, (7) shows how the rod interfaces with the gantry.



I imagine you could set the amount of rotation quite easily by hand, by moving the camera to each end of the rail, and adjusting it so that it remains locked on the subject. (Or otherwise, if you want what they call ‘panorama shooting’).

This passive mechanical method would certainly save on complexity if I could make something similar work.

WIP: I think for version 1 I might just put this whole problem aside and have a non-rotating gantry

### Synchronising time-lapse shutter release with motion

From this review on a commercial slider:  <https://www.amazon.co.uk/gp/customer-reviews/RDGLTSU4YIVCB/ref=cm_cr_dp_d_rvw_ttl?ie=UTF8&ASIN=B07BMLD4N4>

> On the timelapse setting, if you set a pause of, say, 2, seconds, it stops for 2 seconds, and then takes the picture at the point it starts moving again. This is a little insane. It needs to stop, take the picture at the *start* of the 2s gap, and then move. It must be still for the whole duration of the picture, obviously.

It sounds like this slider also lets you control the shutter release on the camera. Which could be a nice feature, but is more than I'm trying to do here. Nevertheless, it might be important to try and synchronise shutter release with points when the gantry is stationary – if indeed there are any with the kind of motion control I end up using.

WIP: I think I'm going to leave this until I have something built.

### Adjusting the gantry so it slides well on the rails

The [Ratrig V-Slider DIY Camera Slider kit](https://ooznest.co.uk/product/v-slider-diy-camera-slider/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) solves this problem by mounting the gantry with eccentric spacers – shims with off-centre holes that can be rotated to position the hole (and therefore the wheel) differently. Too loose a fit and the gantry will be unstable, too tight and there may be too much friction. Either problem could result in jerky movement.

A common solution in furniture design is to mount fixings into slots. This might be a simpler method, needing fewer specialised parts, but is also less finely adjustable.

### Providing user controls and feedback

WIP

### Stopping the motor when the slider reaches the end of the rail.

WIP

<!--

Parts

Timing belt and pulley
https://learn.adafruit.com/bluetooth-motorized-camera-slider/overview
> A GT2 timing pulley mounted to the stepper motor and a radial ball bearing allows a GT2 timing belt to pull the platform across the support slide rail.   

https://www.adafruit.com/product/1184
Timing Belt GT2 Profile - 2mm pitch - 6mm wide 1164mm long (582 teeth on a 2mm tooth pitch)

![](Camera%20Slider%20page%201/gt2tooth.jpg)

#Camera Slider#
 -->

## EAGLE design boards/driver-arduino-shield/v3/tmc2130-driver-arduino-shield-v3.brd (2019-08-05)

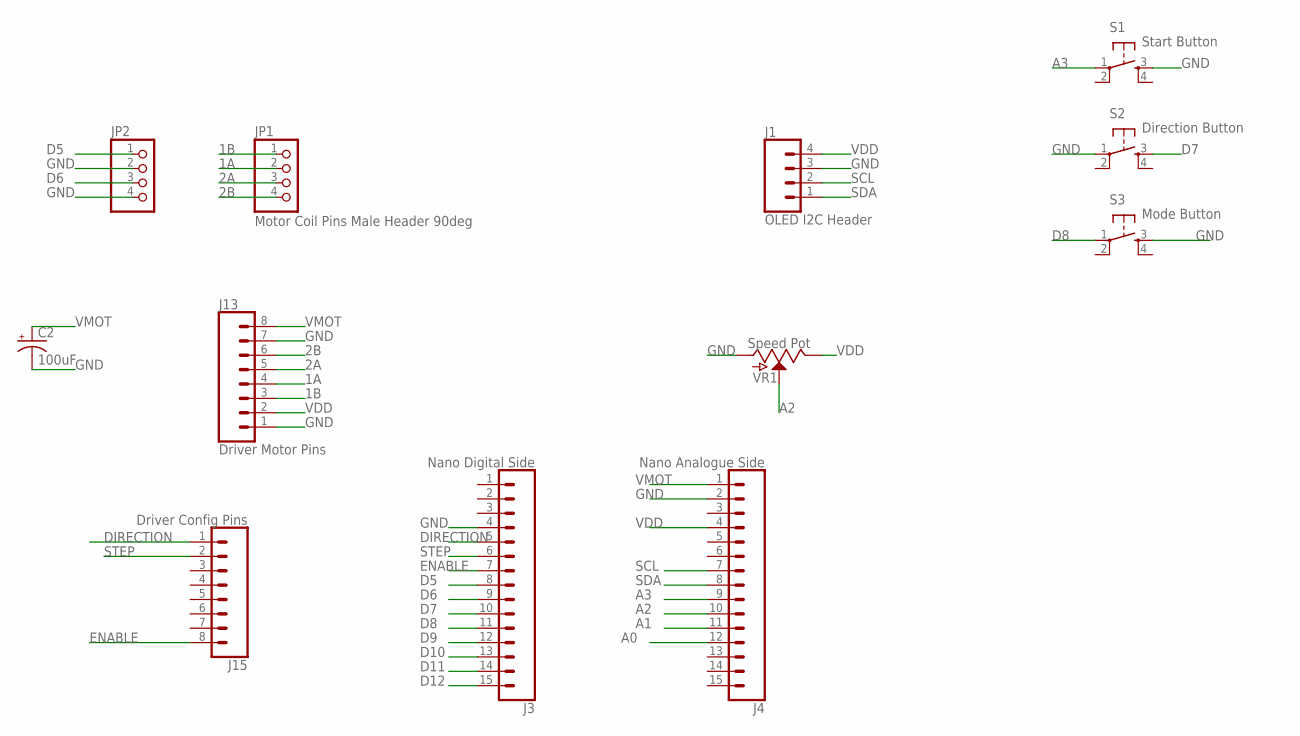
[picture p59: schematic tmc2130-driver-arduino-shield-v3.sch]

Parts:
C2: 100uF; CPOL-RADIAL-2.5MM-6.5MM
J1: OLED I2C Header; 1X04_LONGPADS
J3: Nano Digital Side; 1X15
J4: Nano Analogue Side; 1X15
J13: Driver Motor Pins; 1X08_LONGPADS
J15: Driver Config Pins; 1X08_LONGPADS
JP1: Motor Coil Pins Male Header 90deg; 1X04/90
JP2: PINHD-1X4/90; 1X04/90
S1: Start Button; 6MM_SWITCH
S2: Direction Button; 6MM_SWITCH
S3: Mode Button; 6MM_SWITCH
VR1: Speed Pot; POT-PTH-ALPS

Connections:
1A: J13.4, JP1.2
1B: J13.3, JP1.1
2A: J13.5, JP1.3
2B: J13.6, JP1.4
A0: J4.12
A1: J4.11
A2: J4.10, VR1.P$2 (S)
A3: J4.9, S1.1
D5: J3.8, JP2.1
D6: J3.9, JP2.3
D7: J3.10, S2.3 (S)
D8: J3.11, S3.1
D9: J3.12
D10: J3.13
D11: J3.14
D12: J3.15
DIRECTION: J3.5, J15.1
ENABLE: J3.7, J15.8
GND: C2.2 (-), J1.3, J3.4, J4.2, J13.1, J13.7, JP2.2, JP2.4, S1.3 (S), S2.1, S3.3 (S), VR1.P$3 (A)
SCL: J1.2, J4.7
SDA: J1.1, J4.8
STEP: J3.6, J15.2
VDD: J1.4, J4.4, J13.2, VR1.P$1 (E)
VMOT: C2.1 (+), J4.1, J13.8

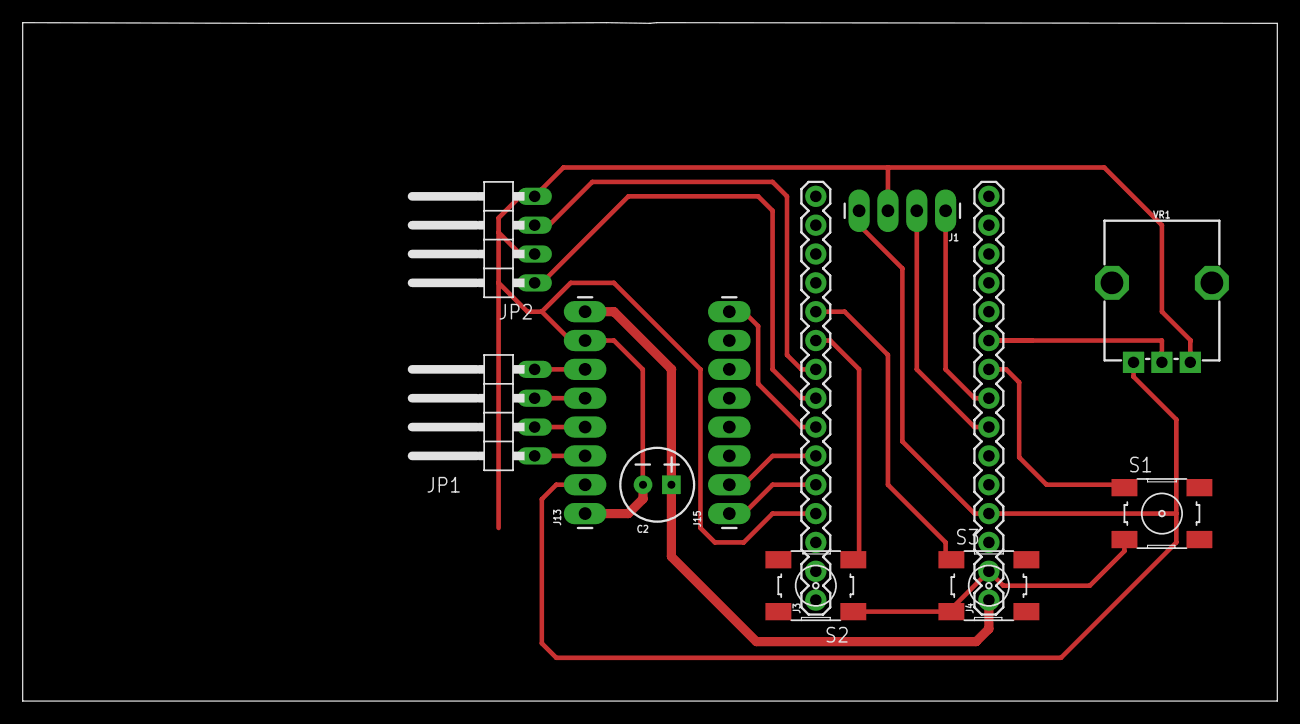
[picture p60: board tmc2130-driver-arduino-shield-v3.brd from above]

Board: 2 copper layers, 110.5 x 59.7 mm, 12 parts (0 on the bottom side), 18 nets.

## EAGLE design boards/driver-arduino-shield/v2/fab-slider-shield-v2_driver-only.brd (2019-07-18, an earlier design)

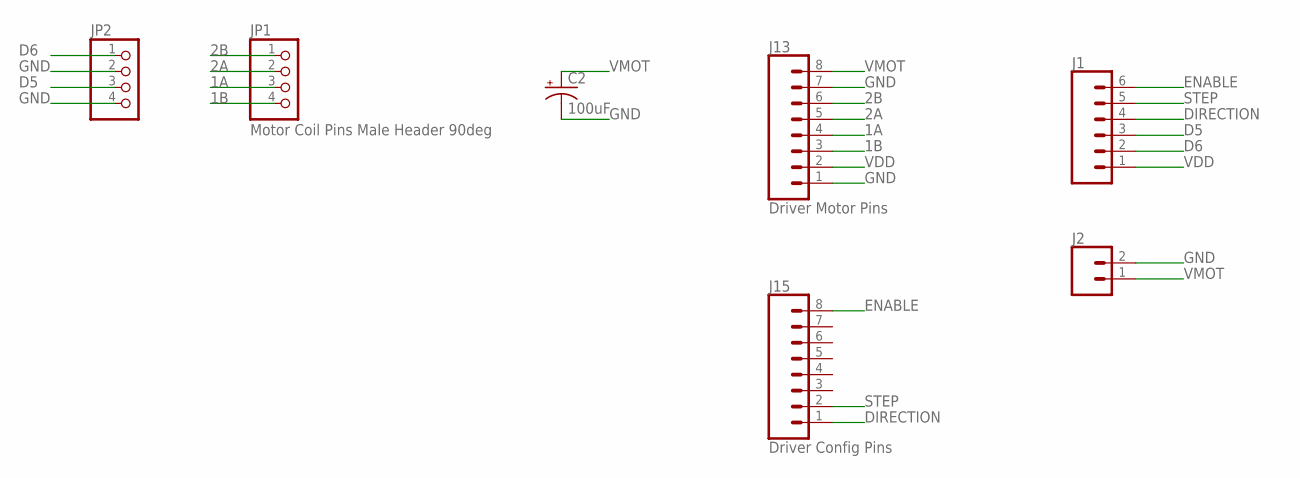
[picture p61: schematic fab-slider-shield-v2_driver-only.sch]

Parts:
C2: 100uF; CPOL-RADIAL-2.5MM-6.5MM
J1: CONN_06LONGPADS; 1X06_LONGPADS
J2: CONN_02PTH3; 1X02_LONGPADS
J13: Driver Motor Pins; 1X08_LONGPADS
J15: Driver Config Pins; 1X08_LONGPADS
JP1: Motor Coil Pins Male Header 90deg; 1X04/90
JP2: PINHD-1X4/90; 1X04/90

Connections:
1A: J13.4, JP1.3
1B: J13.3, JP1.4
2A: J13.5, JP1.2
2B: J13.6, JP1.1
D5: J1.3, JP2.3
D6: J1.2, JP2.1
DIRECTION: J1.4, J15.1
ENABLE: J1.6, J15.8
GND: C2.2 (-), J2.2, J13.1, J13.7, JP2.2, JP2.4
STEP: J1.5, J15.2
VDD: J1.1, J13.2
VMOT: C2.1 (+), J2.1, J13.8

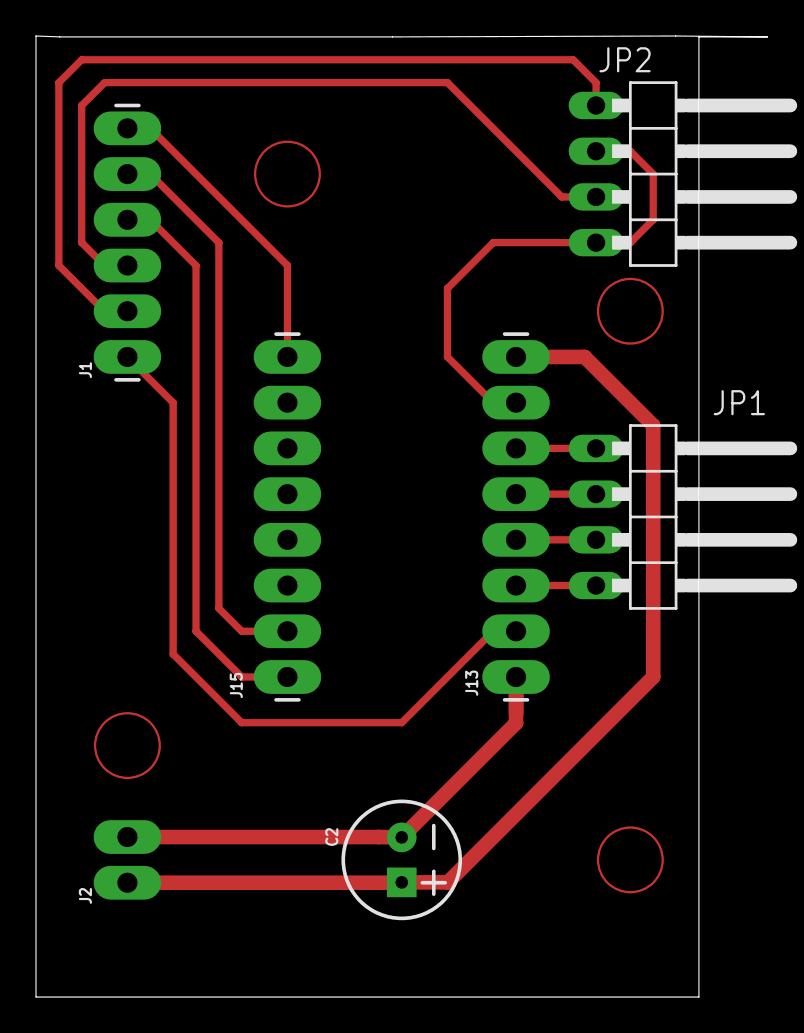
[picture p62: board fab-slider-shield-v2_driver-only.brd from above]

Board: 2 copper layers, 40.6 x 53.4 mm, 7 parts (0 on the bottom side), 12 nets.

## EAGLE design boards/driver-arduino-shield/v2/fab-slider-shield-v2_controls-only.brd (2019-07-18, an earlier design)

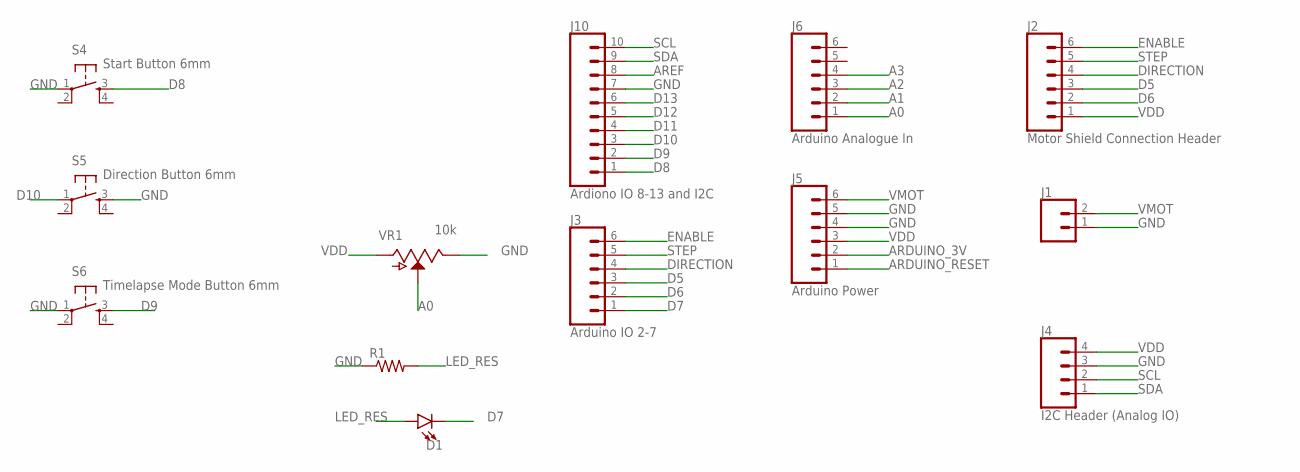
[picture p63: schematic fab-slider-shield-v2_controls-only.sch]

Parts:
D1: LED1206; LED-1206
J1: CONN_02PTH3; 1X02_LONGPADS
J2: Motor Shield Connection Header; 1X06_LONGPADS
J3: Arduino IO 2-7; 1X06_NO_SILK
J4: I2C Header (Analog IO); 1X04
J5: Arduino Power; 1X06_NO_SILK
J6: Arduino Analogue In; 1X06_NO_SILK
J10: Ardiono IO 8-13 and I2C; 1X10_NO_SILK
R1: RES-US1206FAB; R1206FAB
S4: Start Button 6mm; 6MM_SWITCH
S5: Direction Button 6mm; 6MM_SWITCH
S6: Timelapse Mode Button 6mm; 6MM_SWITCH
VR1: 10k; POT-PTH-ALPS

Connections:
A0: J6.1, VR1.P$2 (S)
A1: J6.2
A2: J6.3
A3: J6.4
ARDUINO_3V: J5.2
ARDUINO_RESET: J5.1
AREF: J10.8
D5: J2.3, J3.3
D6: J2.2, J3.2
D7: D1.C, J3.1
D8: J10.1, S4.3 (S)
D9: J10.2, S6.3 (S)
D10: J10.3, S5.1
D11: J10.4
D12: J10.5
D13: J10.6
DIRECTION: J2.4, J3.4
ENABLE: J2.6, J3.6
GND: J1.1, J4.3, J5.4, J5.5, J10.7, R1.1, S4.1, S5.3 (S), S6.1, VR1.P$1 (E)
LED_RES: D1.A, R1.2
SCL: J4.2, J10.10
SDA: J4.1, J10.9
STEP: J2.5, J3.5
VDD: J2.1, J4.4, J5.3, VR1.P$3 (A)
VMOT: J1.2, J5.6

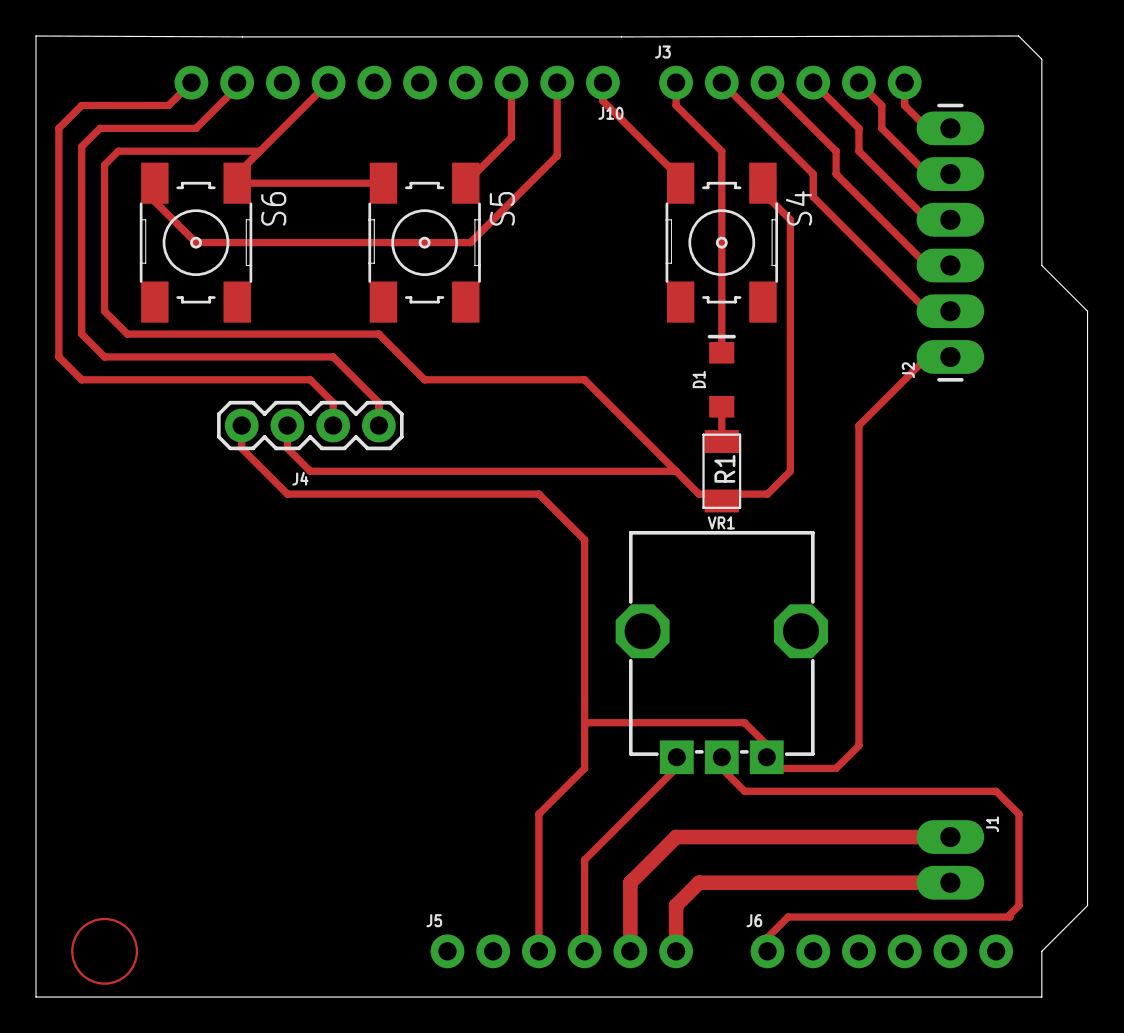
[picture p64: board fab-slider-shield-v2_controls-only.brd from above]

Board: 2 copper layers, 58.4 x 53.4 mm, 13 parts (0 on the bottom side), 16 nets.

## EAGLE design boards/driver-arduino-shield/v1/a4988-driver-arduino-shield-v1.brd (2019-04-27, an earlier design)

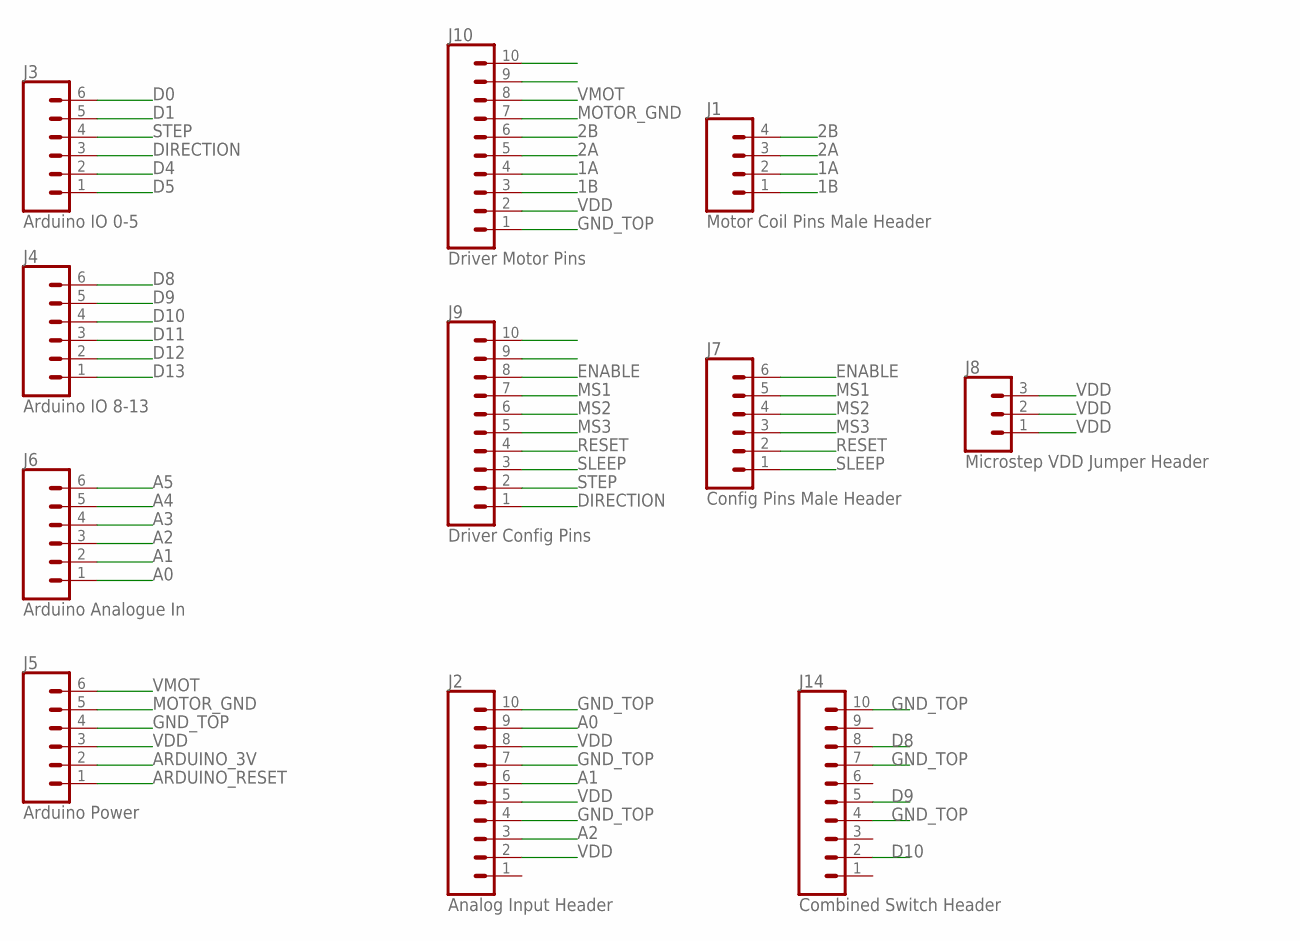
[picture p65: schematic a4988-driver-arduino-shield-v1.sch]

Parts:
J1: Motor Coil Pins Male Header; 1X04_LONGPADS
J2: Analog Input Header; 1X10_SMD_MALE
J3: Arduino IO 0-5; 1X06_NO_SILK
J4: Arduino IO 8-13; 1X06_NO_SILK
J5: Arduino Power; 1X06_NO_SILK
J6: Arduino Analogue In; 1X06_NO_SILK
J7: Config Pins Male Header; 1X06_SMD_MALE
J8: Microstep VDD Jumper Header; 1X03_LONGPADS
J9: Driver Config Pins; 1X10_SMD_MALE
J10: Driver Motor Pins; 1X10_SMD_MALE
J14: Combined Switch Header; 1X10_SMD_MALE

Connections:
1A: J1.2, J10.4
1B: J1.1, J10.3
2A: J1.3, J10.5
2B: J1.4, J10.6
A0: J2.9, J6.1
A1: J2.6, J6.2
A2: J2.3, J6.3
A3: J6.4
A4: J6.5
A5: J6.6
ARDUINO_3V: J5.2
ARDUINO_RESET: J5.1
D0: J3.6
D1: J3.5
D4: J3.2
D5: J3.1
D8: J4.6, J14.8
D9: J4.5, J14.5
D10: J4.4, J14.2
D11: J4.3
D12: J4.2
D13: J4.1
DIRECTION: J3.3, J9.1
ENABLE: J7.6, J9.8
GND_TOP: J2.4, J2.7, J2.10, J5.4, J10.1, J14.4, J14.7, J14.10
MOTOR_GND: J5.5, J10.7
MS1: J7.5, J9.7
MS2: J7.4, J9.6
MS3: J7.3, J9.5
RESET: J7.2, J9.4
SLEEP: J7.1, J9.3
STEP: J3.4, J9.2
VDD: J2.2, J2.5, J2.8, J5.3, J8.1, J8.2, J8.3, J10.2
VMOT: J5.6, J10.8

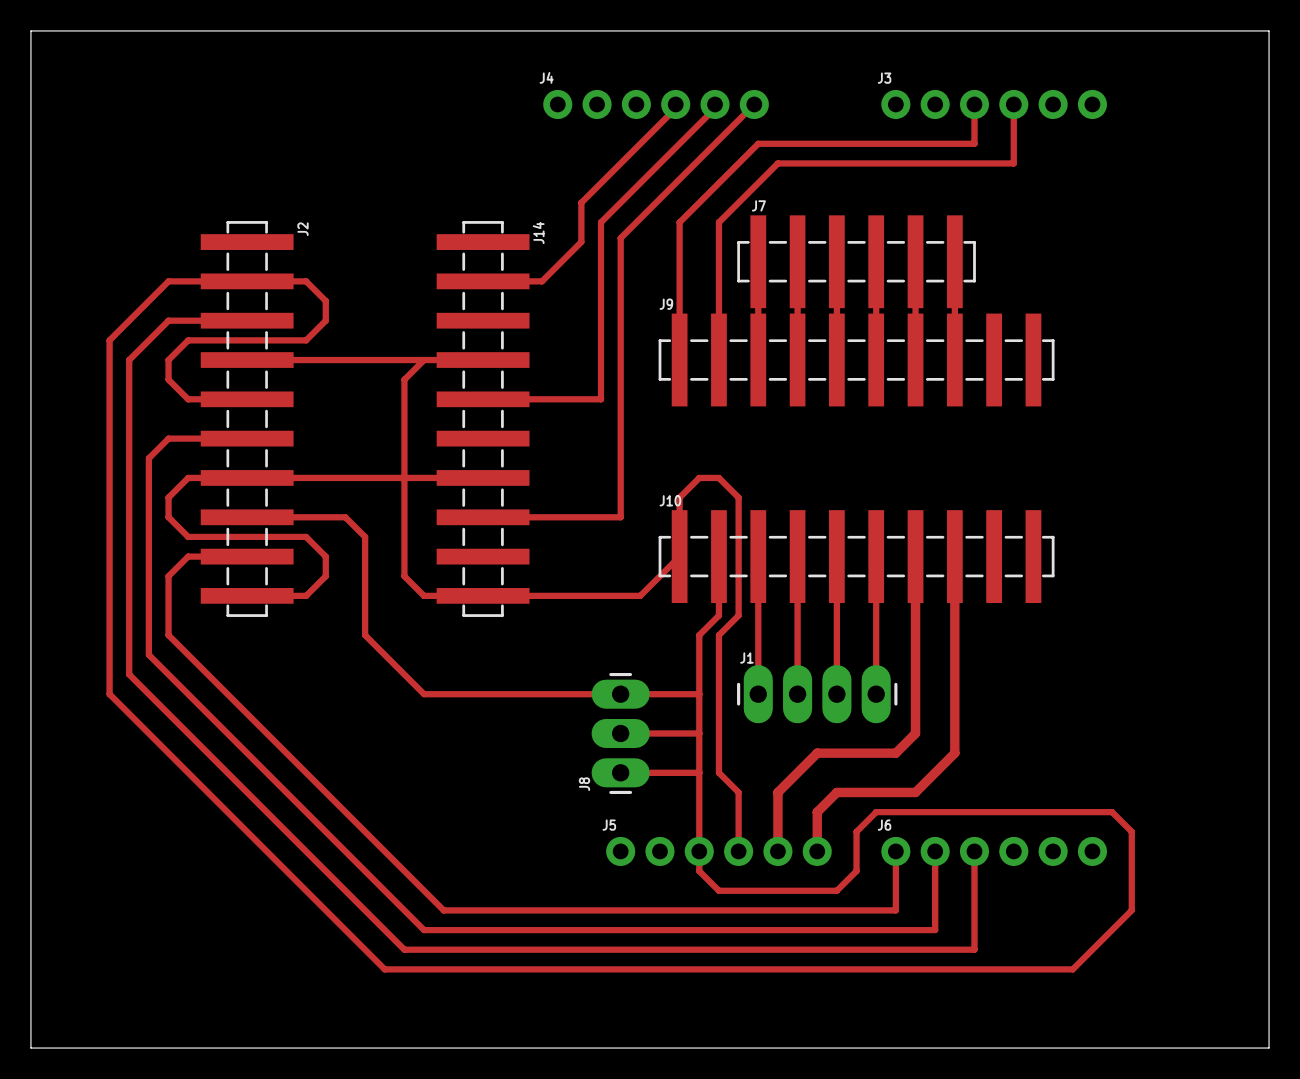
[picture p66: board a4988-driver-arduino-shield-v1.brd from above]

Board: 2 copper layers, 80.0 x 65.7 mm, 11 parts (0 on the bottom side), 22 nets.

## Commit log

2019-04-27 V1 board design for driver shield
    [a4988-driver-arduino-shield-v1.brd, a4988-driver-arduino-shield-v1.sch]
2019-04-27 add supplementary files for driver shield
2019-04-28 board pictures
2019-04-28 add gantry 3D parts
    [gantry-d-ring-coverplate.stl, gantry.stl]
2019-04-28 add 3d parts
    [end-cap-2D.dxf, end-cap-3D.stl, gantry-d-ring-coverplate.stl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]
2019-04-28 tidy 3D parts
    [end-cap-2D.dxf, end-cap-3D.stl]
2019-04-28 add end stop clip
    [endstop_mount_mirrored.stl]
2019-04-28 Add 2D files for idler pulley plate
    [idler-pulley-plate.dxf]
2019-04-30 add motor bracket
    [motor-bracket.stl]
2019-04-30 add assembly files
    [fab-slider-v1.f3z]
2019-04-30 endstop assets
2019-05-04 motor bracket docs
2019-05-22 update current adjustments
2019-05-30 move boards into v1/
    [a4988-driver-arduino-shield-v1.brd, a4988-driver-arduino-shield-v1.sch]
2019-05-30 move more board files into v1/
2019-07-17 add tmc2130 driver page
2019-07-18 Add v2 shield designs
    [fab-slider-shield-v2_controls-only.brd, fab-slider-shield-v2_controls-only.sch, fab-slider-shield-v2_driver-only.brd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]
2019-08-05 add faceplate files
    [flat-electronics-faceplate.dxf]
2019-08-05 Add v3 shield design
    [tmc2130-driver-arduino-shield-v3.brd, tmc2130-driver-arduino-shield-v3.sch]
2019-08-09 board diagrams, oled mount, photos
    [oled-mount.stl]
2019-08-09 board v3 photos
2019-08-09 arduino readmes

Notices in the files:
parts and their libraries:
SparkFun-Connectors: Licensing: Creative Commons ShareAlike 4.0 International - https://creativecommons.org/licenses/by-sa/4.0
